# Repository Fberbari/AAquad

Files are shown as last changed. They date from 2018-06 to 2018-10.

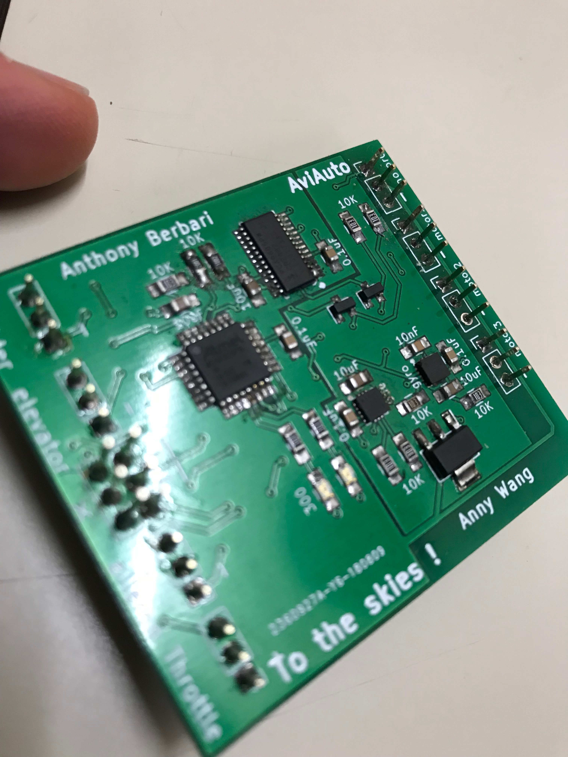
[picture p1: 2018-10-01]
pic_1.jpeg

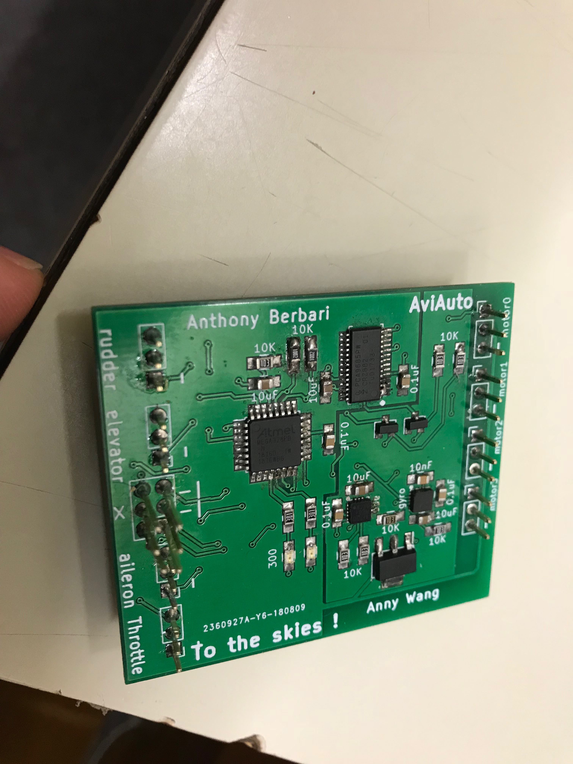
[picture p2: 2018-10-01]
pic_2.jpeg

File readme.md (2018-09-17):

This is an implementation of a quadcopter filght computer running baremetal on an atmega 328pb chip that takes input a standard hobby receiver and outputs pwm to esc's.

These directories contain the full firmware and the pcb design + gerber files.

As of right now, the system produces desirable results and has passed some basic functionality tests. 
I am currently waiting on a mechanical engineering student to finish designing the frame of the aircraft before further testing.

WORKING PRINCIPLE

	As of right now, the system reads input from the receiver via an interrupt based (asynchronous approach). This, because of the 50Hz pwm encoding that the receiver emits is by far the slowest process.

	Apart from this step, the rest of the processis synchronous and the loop goesas follows:

		1. The processor gathers data from the 2 on board sensors (accelerometer and gyroscope) via I2C.
		2. Using a modified version of the Kallman filter, the processor uses both pieces of data to determine the absolute position of the aircraft (with reference to gravity)
		3. A function gathers all the newest available data from the pilot and computes the pilots intention. (How should the aircraft bank and pitch and how strong should 		motor power be)
		4. A PID algorythim then uses the processed sensor data aswell, the processed pilot data and the previous cycle's data to compute 4 numbers that represent the 				percentage of full power that each motor should run at to best achieve the pilot's wishes
		5. Those numbers are encodedinto values that the pwm chip can understand and sent to it via I2C.
		6. The process repeats

PURPOSE

	The purose of this project was to familiarize myself with the basics of avr architecture, firmware design flow, communications between chips (I2C), pcb design flow etc.
	It was also a way to enter the world of embedded design in aviation. 

I (Anthony Berbari) AM SOLELY RESPONSIBLE FOR ALL THE FIRMWARE AND HARDWARE DESIGN DONE ON THIS PROJECT.

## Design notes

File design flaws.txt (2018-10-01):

1. each voltage regulator required a 10 uF cap

2. the footprints for the qfn's are far too small and the white squares are missing.

3. The back fin of the power egulators should be connected to the ground plane.

4. An IMU should have been used instead of a seperate acc and gyro.

5. Always use an external pullup resistor for the I2C lines. DO not rely on the software

6. Use the PWM pin todo mux sort of stuff.

7. ALWAYS select the cheapest and least complex approach.

8. The input capture unit (ICU) of the timers should be used to read pwm. 

9. use 2 different I2C busses when using a level shifter

10. spacing between header pins should fit a breadboard.

11. New and improved algos that you used in numerical analysys should be used to approximate the integral and derivative for the PID

NEgotiation genius principles+ECE 209 first lecture integrative thinking should be used

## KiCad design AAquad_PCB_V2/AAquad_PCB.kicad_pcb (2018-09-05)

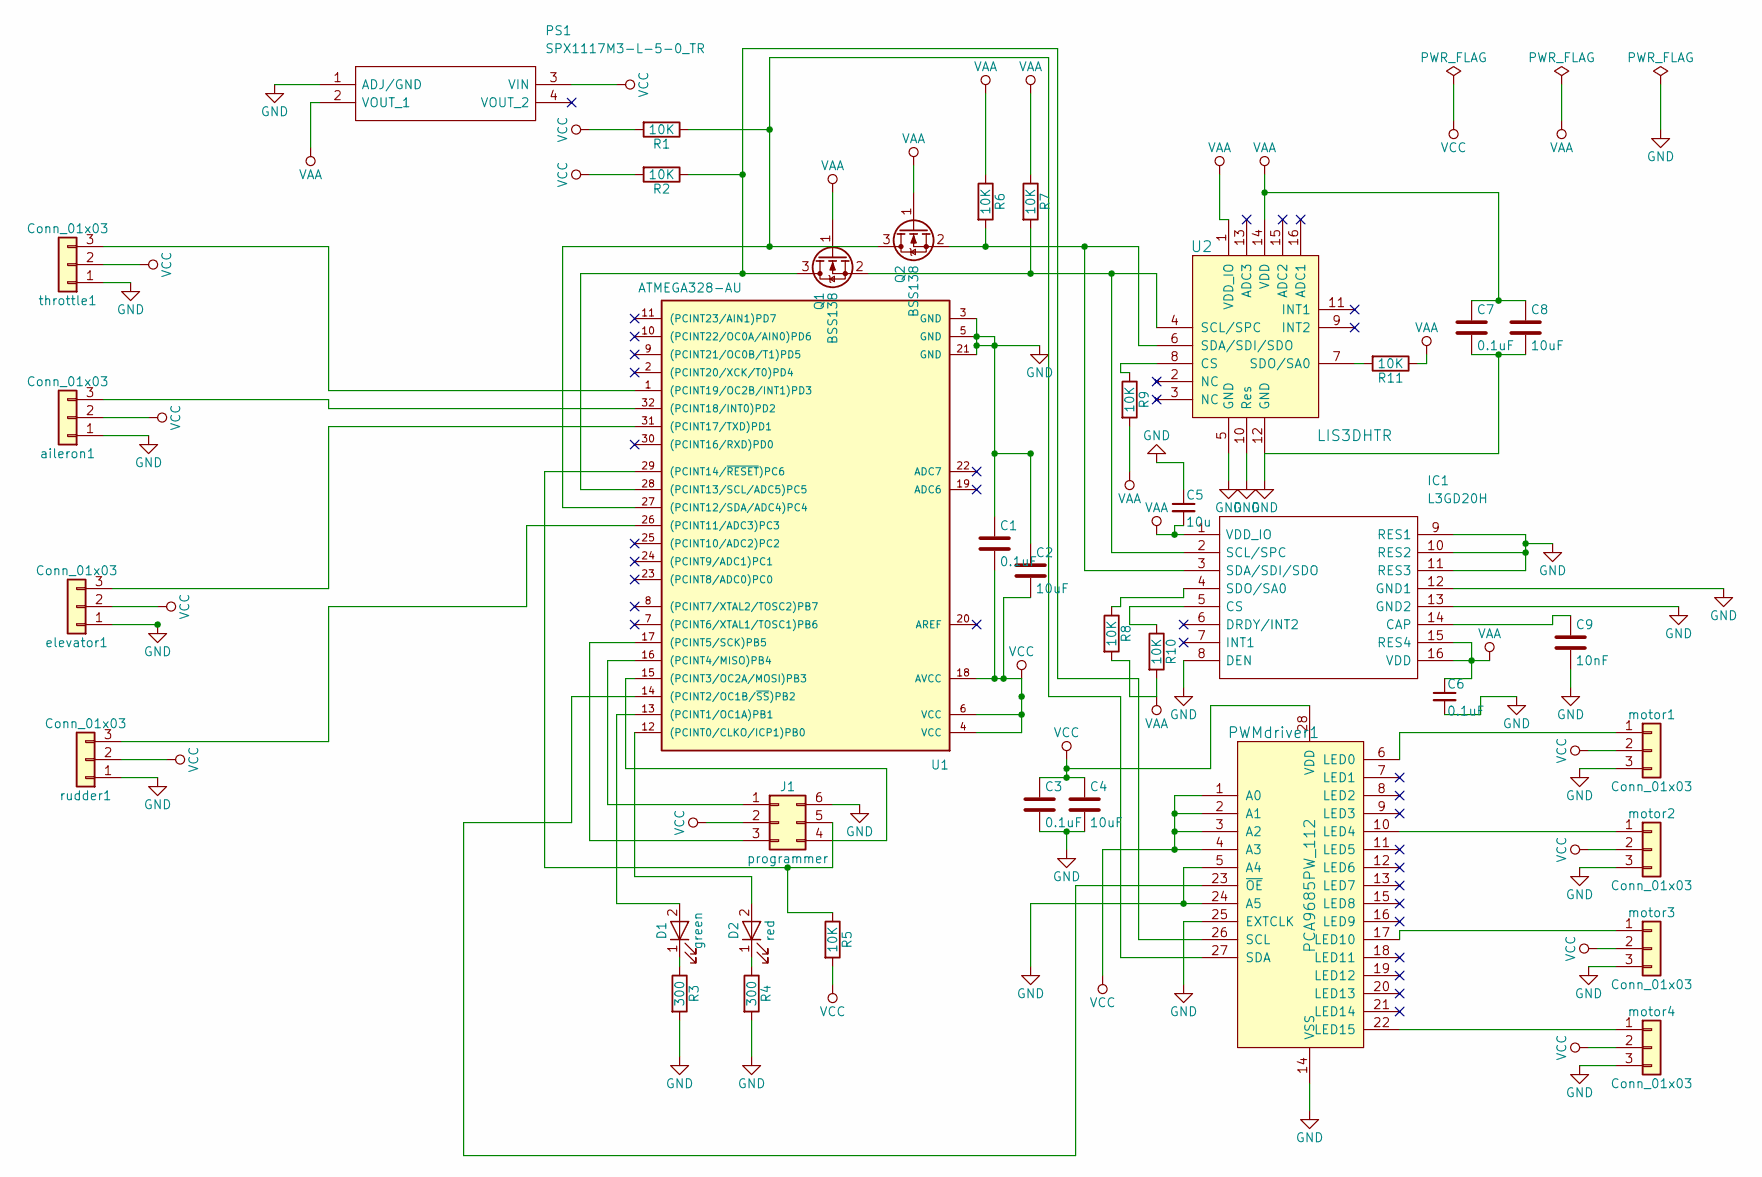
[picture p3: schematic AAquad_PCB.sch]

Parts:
C1, C3, C6, C7: 0.1uF; C_0805_HandSoldering
C2, C4, C8: 10uF; C_0805_HandSoldering
C5: 10u; C_0805_HandSoldering
C9: 10nF; C_0805_HandSoldering
D1: green; LED_0805_HandSoldering
D2: red; LED_0805_HandSoldering
IC1: L3GD20H; L3gd20h; Manufacturer_Part_Number L3GD20H
J1: programmer; Pin_Header_Straight_2x03_Pitch2.54mm
PS1: SPX1117M3-L-5-0_TR; SOT230P700X170-4N; Manufacturer_Part_Number SPX1117M3-L-5-0/TR
PWMdriver1: PCA9685PW_112; TSSOP-28_W4.40mm; MPN PCA9685PW,112; Digi-Key_PN 568-8366-5-ND
Q1, Q2: BSS138; SOT-23
R1, R2, R5, R6, R7, R8, R9, R10, R11: 10K; R_0805_HandSoldering
R3, R4: 300; R_0805_HandSoldering
U1: ATMEGA328-AU; TQFP-32_7x7mm_Pitch0.8mm
U2: LIS3DHTR; Lis3dh; MPN LIS3DHTR; Digi-Key_PN 497-10613-1-ND
aileron1: Conn_01x03; Pin_Header_Straight_1x03_Pitch2.54mm
elevator1: Conn_01x03; Pin_Header_Straight_1x03_Pitch2.54mm
motor1, motor2, motor3, motor4: Conn_01x03; Pin_Header_Straight_1x03_Pitch2.54mm
rudder1: Conn_01x03; Pin_Header_Straight_1x03_Pitch2.54mm
throttle1: Conn_01x03; Pin_Header_Straight_1x03_Pitch2.54mm

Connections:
GND: C1.1, C2.1, C3.2, C4.2, C5.1, C6.2, C7.2, C8.2, C9.2, IC1.8 (DEN), IC1.9 (RES1), IC1.10 (RES2), IC1.11 (RES3), IC1.12 (GND1), IC1.13 (GND2), J1.6, PS1.1 (ADJ/GND), PWMdriver1.5 (A4), PWMdriver1.14 (VSS), PWMdriver1.24 (A5), PWMdriver1.25 (EXTCLK), R3.2, R4.2, U1.3 (GND), U1.5 (GND), U1.21 (GND), U2.5 (GND), U2.10 (Res), U2.12 (GND), aileron1.1, elevator1.1, motor1.3, motor2.3, motor3.3, motor4.3, rudder1.1, throttle1.1
unnamed: C9.1, IC1.14 (CAP)
unnamed: D1.1 (K), R3.1
unnamed: D1.2 (A), U1.13 ((PCINT1/OC1A)PB1)
unnamed: D2.1 (K), R4.1
unnamed: D2.2 (A), U1.12 ((PCINT0/CLKO/ICP1)PB0)
unnamed: IC1.2 (SCL/SPC), Q1.2 (S), R7.2, U2.4 (SCL/SPC)
unnamed: IC1.3 (SDA/SDI/SDO), Q2.2 (S), R6.2, U2.6 (SDA/SDI/SDO)
unnamed: IC1.4 (SDO/SA0), R8.1
unnamed: IC1.5 (CS), R10.1
unnamed: J1.1, U1.16 ((PCINT4/MISO)PB4)
unnamed: J1.3, U1.17 ((PCINT5/SCK)PB5)
unnamed: J1.4, U1.15 ((PCINT3/OC2A/MOSI)PB3)
unnamed: J1.5, R5.1, U1.29 ((PCINT14/~RESET~)PC6)
unnamed: PWMdriver1.6 (LED0), motor1.1
unnamed: PWMdriver1.10 (LED4), motor2.1
unnamed: PWMdriver1.17 (LED10), motor3.1
unnamed: PWMdriver1.22 (LED15), motor4.1
unnamed: PWMdriver1.23 (~OE), U1.14 ((PCINT2/OC1B/~SS~)PB2)
unnamed: PWMdriver1.26 (SCL), Q1.3 (D), R2.1, U1.28 ((PCINT13/SCL/ADC5)PC5)
unnamed: PWMdriver1.27 (SDA), Q2.3 (D), R1.1, U1.27 ((PCINT12/SDA/ADC4)PC4)
unnamed: R9.1, U2.8 (CS)
unnamed: R11.2, U2.7 (SDO/SA0)
unnamed: U1.1 ((PCINT19/OC2B/INT1)PD3), throttle1.3
unnamed: U1.26 ((PCINT11/ADC3)PC3), rudder1.3
unnamed: U1.31 ((PCINT17/TXD)PD1), elevator1.3
unnamed: U1.32 ((PCINT18/INT0)PD2), aileron1.3
VAA: C5.2, C6.1, C7.1, C8.1, IC1.1 (VDD_IO), IC1.15 (RES4), IC1.16 (VDD), PS1.2 (VOUT_1), Q1.1 (G), Q2.1 (G), R6.1, R7.1, R8.2, R9.2, R10.2, R11.1, U2.1 (VDD_IO), U2.14 (VDD)
VCC: C1.2, C2.2, C3.1, C4.1, J1.2, PS1.3 (VIN), PWMdriver1.1 (A0), PWMdriver1.2 (A1), PWMdriver1.3 (A2), PWMdriver1.4 (A3), PWMdriver1.28 (VDD), R1.2, R2.2, R5.2, U1.4 (VCC), U1.6 (VCC), U1.18 (AVCC), aileron1.2, elevator1.2, motor1.2, motor2.2, motor3.2, motor4.2, rudder1.2, throttle1.2

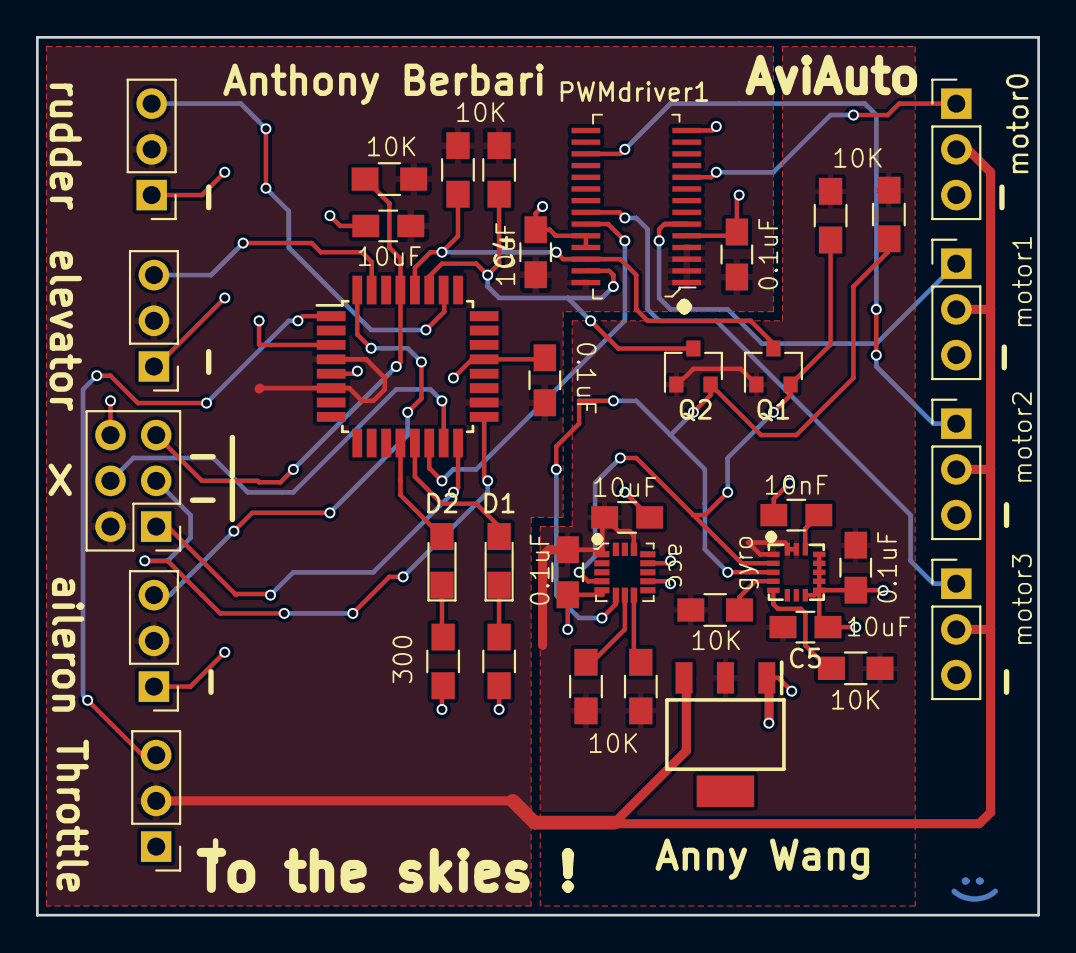
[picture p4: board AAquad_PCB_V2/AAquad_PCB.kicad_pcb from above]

Board: 2 copper layers, 55.6 x 48.8 mm, 38 parts (0 on the bottom side), 29 nets.

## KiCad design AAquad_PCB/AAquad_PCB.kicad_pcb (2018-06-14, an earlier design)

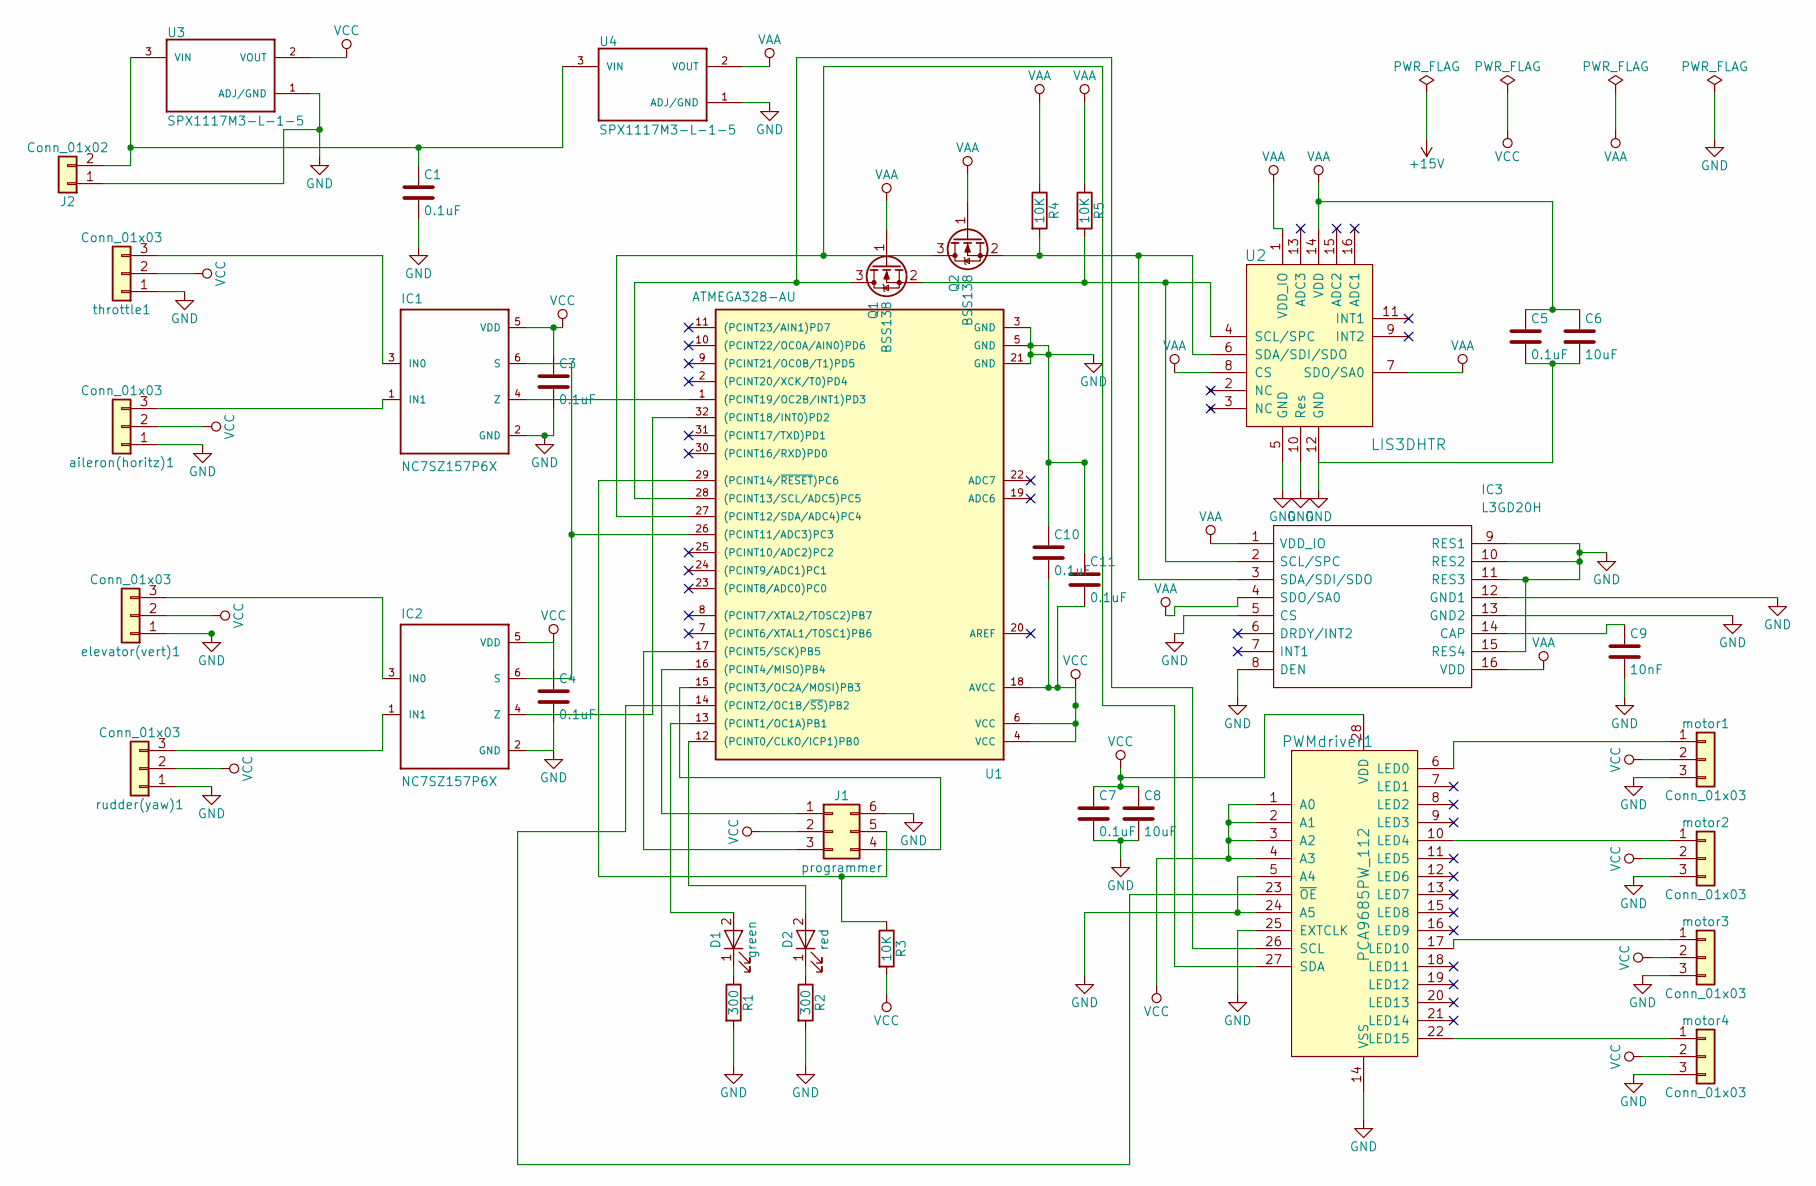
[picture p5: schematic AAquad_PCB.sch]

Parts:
C1, C3, C4, C5, C7, C10, C11: 0.1uF; C_0805_HandSoldering
C6, C8: 10uF; C_0805_HandSoldering
C9: 10nF; C_0805_HandSoldering
D1: green; LED_0805_HandSoldering
D2: red; LED_0805_HandSoldering
IC1, IC2: NC7SZ157P6X; SOT65P210X110-6N
IC3: L3GD20H; LGA(3X3X1.0-16L); Manufacturer_Part_Number L3GD20H
J1: programmer; Pin_Header_Angled_2x03_Pitch2.54mm
J2: Conn_01x02; Pin_Header_Angled_1x02_Pitch2.54mm
PWMdriver1: PCA9685PW_112; TSSOP-28_W4.40mm; MPN PCA9685PW,112; Digi-Key_PN 568-8366-5-ND
Q1, Q2: BSS138; SOT-23
R1, R2: 300; R_0805_HandSoldering
R3, R4, R5: 10K; R_0805_HandSoldering
U1: ATMEGA328-AU; TQFP-32_7x7mm_Pitch0.8mm
U2: LIS3DHTR; VFLGA-16_3x3mm; MPN LIS3DHTR; Digi-Key_PN 497-10613-1-ND
U3, U4: SPX1117M3-L-1-5; SOT230P700X180-3N
aileron(horitz)1: Conn_01x03; Pin_Header_Angled_1x03_Pitch2.54mm
elevator(vert)1: Conn_01x03; Pin_Header_Angled_1x03_Pitch2.54mm
motor1, motor2, motor3, motor4: Conn_01x03; Pin_Header_Angled_1x03_Pitch2.54mm
rudder(yaw)1: Conn_01x03; Pin_Header_Angled_1x03_Pitch2.54mm
throttle1: Conn_01x03; Pin_Header_Angled_1x03_Pitch2.54mm

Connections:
GND: C1.2, C3.2, C4.2, C5.2, C6.2, C7.2, C8.2, C9.2, C10.1, C11.1, IC1.2 (GND), IC2.2 (GND), IC3.5 (CS), IC3.8 (DEN), IC3.9 (RES1), IC3.10 (RES2), IC3.11 (RES3), IC3.12 (GND1), IC3.13 (GND2), IC3.15 (RES4), J1.6, J2.1, PWMdriver1.5 (A4), PWMdriver1.14 (VSS), PWMdriver1.24 (A5), PWMdriver1.25 (EXTCLK), R1.2, R2.2, U1.3 (GND), U1.5 (GND), U1.21 (GND), U2.5 (GND), U2.10 (Res), U2.12 (GND), U3.1 (ADJ/GND), U4.1 (ADJ/GND), aileron(horitz)1.1, elevator(vert)1.1, motor1.3, motor2.3, motor3.3, motor4.3, rudder(yaw)1.1, throttle1.1
unnamed: C1.1, J2.2, U3.3 (VIN), U4.3 (VIN)
unnamed: C9.1, IC3.14 (CAP)
unnamed: D1.1 (K), R1.1
unnamed: D1.2 (A), U1.13 ((PCINT1/OC1A)PB1)
unnamed: D2.1 (K), R2.1
unnamed: D2.2 (A), U1.12 ((PCINT0/CLKO/ICP1)PB0)
unnamed: IC1.1 (IN1), aileron(horitz)1.3
unnamed: IC1.3 (IN0), throttle1.3
unnamed: IC1.4 (Z), U1.1 ((PCINT19/OC2B/INT1)PD3)
unnamed: IC1.6 (S), IC2.6 (S), U1.26 ((PCINT11/ADC3)PC3)
unnamed: IC2.1 (IN1), rudder(yaw)1.3
unnamed: IC2.3 (IN0), elevator(vert)1.3
unnamed: IC2.4 (Z), U1.32 ((PCINT18/INT0)PD2)
unnamed: IC3.2 (SCL/SPC), Q1.2 (S), R5.2, U2.4 (SCL/SPC)
unnamed: IC3.3 (SDA/SDI/SDO), Q2.2 (S), R4.2, U2.6 (SDA/SDI/SDO)
unnamed: J1.1, U1.16 ((PCINT4/MISO)PB4)
unnamed: J1.3, U1.17 ((PCINT5/SCK)PB5)
unnamed: J1.4, U1.15 ((PCINT3/OC2A/MOSI)PB3)
unnamed: J1.5, R3.1, U1.29 ((PCINT14/~RESET~)PC6)
unnamed: PWMdriver1.6 (LED0), motor1.1
unnamed: PWMdriver1.10 (LED4), motor2.1
unnamed: PWMdriver1.17 (LED10), motor3.1
unnamed: PWMdriver1.22 (LED15), motor4.1
unnamed: PWMdriver1.23 (~OE), U1.14 ((PCINT2/OC1B/~SS~)PB2)
unnamed: PWMdriver1.26 (SCL), Q1.3 (D), U1.28 ((PCINT13/SCL/ADC5)PC5)
unnamed: PWMdriver1.27 (SDA), Q2.3 (D), U1.27 ((PCINT12/SDA/ADC4)PC4)
VAA: C5.1, C6.1, IC3.1 (VDD_IO), IC3.4 (SDO/SA0), IC3.16 (VDD), Q1.1 (G), Q2.1 (G), R4.1, R5.1, U2.1 (VDD_IO), U2.7 (SDO/SA0), U2.8 (CS), U2.14 (VDD), U4.2 (VOUT)
VCC: C3.1, C4.1, C7.1, C8.1, C10.2, C11.2, IC1.5 (VDD), IC2.5 (VDD), J1.2, PWMdriver1.1 (A0), PWMdriver1.2 (A1), PWMdriver1.3 (A2), PWMdriver1.4 (A3), PWMdriver1.28 (VDD), R3.2, U1.4 (VCC), U1.6 (VCC), U1.18 (AVCC), U3.2 (VOUT), aileron(horitz)1.2, elevator(vert)1.2, motor1.2, motor2.2, motor3.2, motor4.2, rudder(yaw)1.2, throttle1.2

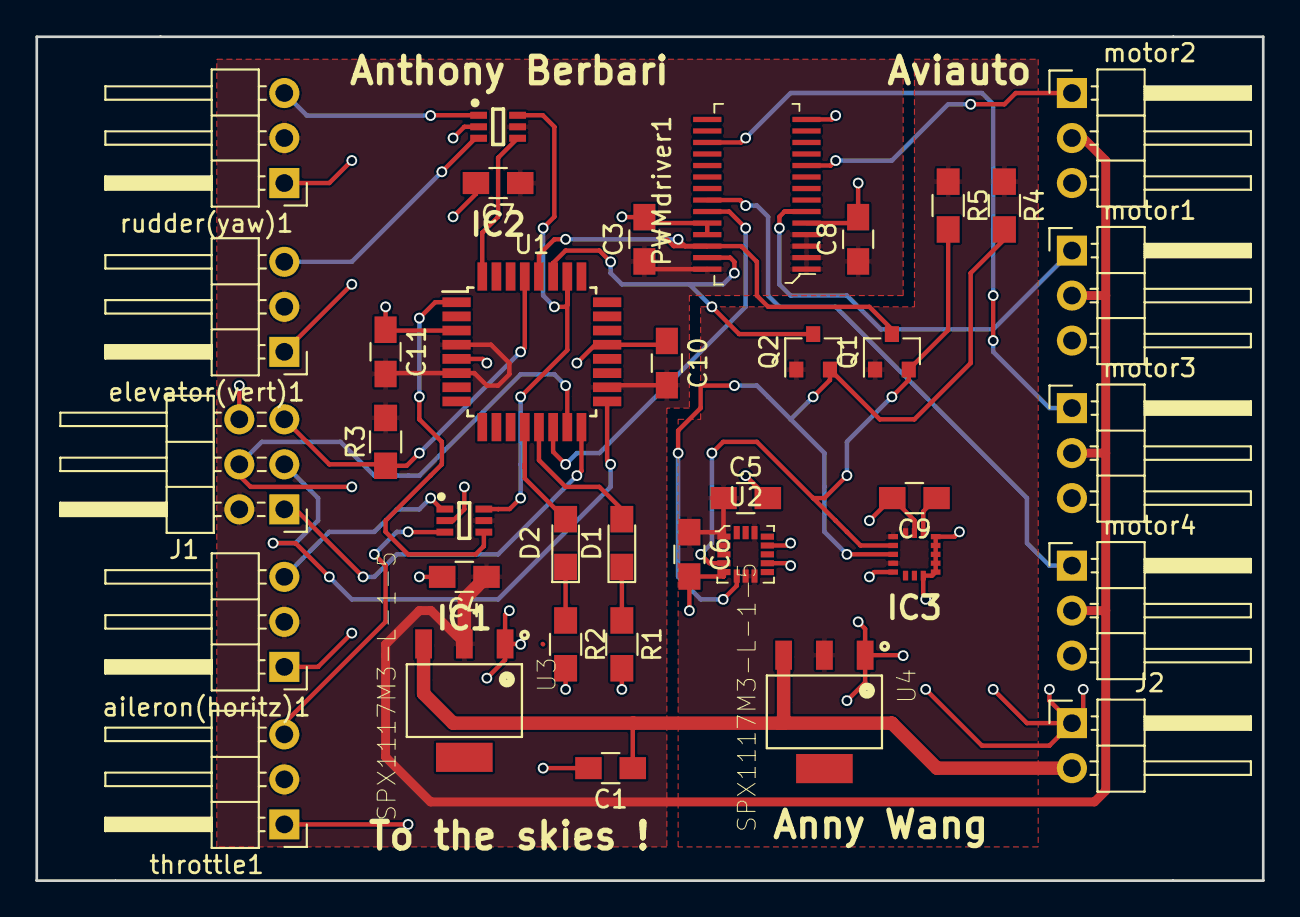
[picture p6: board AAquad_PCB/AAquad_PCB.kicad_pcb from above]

Board: 2 copper layers, 69.2 x 47.6 mm, 37 parts (0 on the bottom side), 29 nets.

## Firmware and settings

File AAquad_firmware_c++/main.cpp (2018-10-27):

/*
 * Firmware Developer : Anthony Berbari
 */ 

#include "avr_compiler.h"



#include "pwm_in_vars.h"	// global external variables



#include "init.h"
#include "I2C_328pb.h"
#include "pilot_instructions.h"
#include "pwm_chip.h"
#include "sensors.h"
#include "bp_PID.h"
#include "combine_data.h"


	
	// These global vars hold raw pilot data. 
	// Requested... holds the time between a rise and fall (or fall and rise). unit used is arbitrary, so long as all is consistent
	// these variables are declared in pwm_in_vars.h and that file is include in main.cpp and in the pilot_instructions.h class
	volatile uint16_t requested_aileron_pos = 0;
	volatile uint16_t requested_elevator_pos = 0;
	volatile uint16_t requested_rudder_pos = 0;
	volatile uint16_t requested_throttle_pos = 0;

	// these store the time stamp of the previous time the associated ISR triggered
	// substracting the time stamp of the previous edge from that of the current edge allows the algorythim to obtain a measure of the pwm's duty cycle.
	// that measure is stored in the above requested.... variables
	volatile uint16_t temp_timer_aileron = 0;
	volatile uint16_t temp_timer_elevator = 0; 
	volatile uint16_t temp_timer_rudder = 0;
	volatile uint16_t temp_timer_throttle = 0; 

	// these are flags that are set true right after the ISR's gather new pilot data
	// they ensure the algorythim that processes it is infact dealing with fresh data
	volatile bool new_aileron_data_available = false;
	volatile bool new_elevator_data_available = false;
	volatile bool new_rudder_data_available = false;
	volatile bool new_throttle_data_available = false;


	// pid objects declaired here to be visible to the ISR
	 pid bank_pid;
	 pid pitch_pid;

	// these global vars are used to exchange data between the ISR that contains the pid algorythim and the main while(1) loop
	volatile float bank_number = 0;
	volatile float pitch_number = 0;
	volatile float throttle_percentage = 0;
	volatile bool  pid_called = false;
	
	


int main(void){
	
	// points to the array that stores the percentage of full each motor should run at
	volatile int* volatile motor_percentages;
	
	
	initialize::timers();
	initialize::interrupts();
	
	// gathers and processes the pilot's wishes
	pilot_instructions pilot;
	pilot.set_max_angle(30);
	pilot.set_max_yaw_rate(45);
	
	//handles all sensor data gathering and processing
	sensors sense;
	
	// initialisation of the chip responsible for talking directly to the esc's
	pwm_chip pwm(121);


	// processes current position and requested position into a number proportional to motor strength
	// This is only for the bank (tilted left or right) angle
	bank_pid.setWeights(1,1,0.5);
	bank_pid.setOutputLimits(-50, 50);

	//Same as on top but for the pitch (tilted forward or back) angle
	pitch_pid.setWeights(1,1,0.5);
	pitch_pid.setOutputLimits(-50, 50);
	


	

	
	// Initialisation finished. Interupts enabled, ready to begin
	sei();
	

	
	while(1){
		
		// sensor data gathered
		sense.read_acc();
		sense.read_gyro();
			
		// all sensor data received and processed
		sense.compute_position();
	
		// all pilot data received and processed
		pilot.compute();	
	
		// pilot commands and sensor data passed to PID object
		pitch_pid.setPoints(pilot.get_pitch_angle(), sense.get_pitch());		
		bank_pid.setPoints(pilot.get_bank_angle(), sense.get_roll());

		//computiations are done
		// the contents of bank_number, pitch_number and throttle power are representative of the pitch and bank required to achieve pilot's wishes
		// these vars are ready to be used by the combine_data method, once the ISR calls it.
		throttle_percentage = pilot.get_throttle_power();
			
		// data_available is only true after a call of the pid loop from the interrupt
		// it is then immediately set to false in wait of the next interrupt	
		if (pid_called){
			
			// results of pid are combined and translated into percentages
			// motor points to an array that contains the percentages that each motor should be run at.
			motor_percentages = combine(bank_number, pitch_number, throttle_percentage);
			
			// data encoded into PWM chip language and sent to the esc's
			pwm.pass( (int*) motor_percentages);	
			pid_called = false;
		}

	}



return 0;

}


ISR(TIMER0_COMPA_vect){

	// PID output recomputed every 0.1s	

		// get the numbers proportional to how strongly we must attempt to bank and pitch to achieve th pilot's wishes 
		bank_number = bank_pid.refresh();
		pitch_number = pitch_pid.refresh();

		// set the flag 
		pid_called = true;
}



// comments for the 4 ISR's to come are the same, so they are only included on this one
// All the following ISR's trigger on any edge
ISR(INT0_vect){
	
		// store the timestamp of the time the edge was detected
		uint16_t temp = TCNT1;
		
		// obviously, the previous edge must have happened before the current edge
		// but because the 16 bit timer may have overflowed and started the count back from 0, we need to check for this
		if ( temp < temp_timer_aileron){

			// the math inside the if condition accounts for a timer overflow
			// the comparison ensures that we only take in new data if that data is reasonable, so  as to not corrupt down the stream algorythyms
			// the values 1110 and 2000 are the lower and upper bounds on what the receiver can output
			if ( ((0xffff - temp_timer_aileron + temp) < 2000) && ((0xffff - temp_timer_aileron + temp) > 1110)){
				
				requested_aileron_pos = (0xffff - temp_timer_aileron) + temp ;

				// since the latest requested aileron position has just been updated, set the flag to true
				new_aileron_data_available = true;
			}
		}

		// this else statement catches the case were no timer overflow has occured
		else {
			
			// the comparisons ensure that we only take in new data if that data is reasonable, so  as to not corrupt down the stream algorythyms
			// the values 1110 and 2000 are the lower and upper bounds on what the receiver can output
			if ( ( (temp - temp_timer_aileron) < 2000) && ( (temp - temp_timer_aileron) > 1110) ) {
	
				requested_aileron_pos = temp - temp_timer_aileron;

				// since the latest requested aileron position has just been updated, set the flag to true
				new_aileron_data_available = true;
			
			}
		}
	
		// no matter what, the current timestamp becomes the previous timestamp
		temp_timer_aileron = temp;

}

ISR(INT1_vect){
	
		uint16_t temp = TCNT1;
		

		if ( temp < temp_timer_throttle){


			if ( ((0xffff - temp_timer_throttle + temp) < 2000) && ((0xffff - temp_timer_throttle + temp) > 1015)){
						
				requested_throttle_pos = (0xffff - temp_timer_throttle) + temp ;
				new_throttle_data_available = true;
			}
		}

		else {
	

			if ( ( (temp - temp_timer_throttle) < 2000) && ( (temp - temp_timer_throttle) > 1015) ) {
						
				requested_throttle_pos = temp - temp_timer_throttle;
				new_throttle_data_available = true;
							
			}
			
		}
	
		
		temp_timer_throttle = temp;
		
		
		
}



ISR(PCINT1_vect){

	uint16_t temp = TCNT1;
		

	if ( temp < temp_timer_rudder){	


		if ( ((0xffff - temp_timer_rudder + temp) < 2000) && ((0xffff - temp_timer_rudder + temp) > 1110)){
						
			requested_rudder_pos = (0xffff - temp_timer_rudder) + temp;
			new_rudder_data_available = true;
		}
	}

	else {	


		if ( ( (temp - temp_timer_rudder) < 2000) && ( (temp - temp_timer_rudder) > 1110) ){
						
			requested_rudder_pos = temp - temp_timer_rudder;
			new_rudder_data_available = true;
						
		}
		
	}

	
	temp_timer_rudder = temp;
	
	

}

ISR(PCINT2_vect){

	uint16_t temp = TCNT1;
	

	if ( temp < temp_timer_elevator){


		if ( ((0xffff - temp_timer_elevator + temp) < 2000) && ((0xffff - temp_timer_elevator + temp) > 1110)){
						
			requested_elevator_pos = (0xffff - temp_timer_elevator) + temp;
			new_elevator_data_available = true;
		}
	}

	else {

		if ( ( (temp - temp_timer_elevator) < 2000) && ( (temp - temp_timer_elevator) > 1110) ) {
						
			requested_elevator_pos = temp - temp_timer_elevator;
			new_elevator_data_available = true;
						
		}
		
	}

	
	temp_timer_elevator = temp;
	
	

}

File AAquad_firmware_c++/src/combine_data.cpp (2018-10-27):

#include "combine_data.h"


int* combine(float bank_number, float pitch_number, float throttle_percentage){

	// the top one is temporary for processing floats whilethe bottom stores the ints
	// bottom one is the one that returns
	float motor[4];
	static int ret_motor[4];

	//inex of motor heavily depends on how the accelerometer and gyro are pointed and how the motors are plugged in.
	motor[0] = (bank_number + pitch_number)  / 2 ;
	motor[1] = (bank_number - pitch_number)  / 2 ;
	motor[2] = (-bank_number + pitch_number) / 2 ;
	motor[3] = (-bank_number - pitch_number) / 2 ;
	
	
	// numbers were in the range [-50, 50], this effectively turns them into a percentage
	// that percentage is the percentage of full power that each motor should turn at.
	for (int i = 0; i < 4; i++){
		
		motor[i] += 50;
	}

	
	// now, that themotors are working correctly relative to each other, multiply by throttle percentage to get the absolute values.
	for (int i = 0; i < 4; i++){
		
		motor[i] *= (throttle_percentage / 80);
	}

	
	// these floats will be cast to integers, so round before hand
	for (int i = 0; i < 4; i++){
		
		ret_motor[i] = round(motor[i]);
	}
	
	
	
	return  ret_motor;

}

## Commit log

2018-07-15 added cart
    [parts(includes_Buzzerboxes).csv]
2018-07-18 built the mux timer init function
2018-07-31 fixed pwm read
2018-08-01 fixed pwm read and fixed timer controll
2018-08-03 interfacing with PWM chip
2018-08-06 began to work on the translating motors branch
2018-08-07 successfull read and processing of PWM on ext_int0
2018-08-22 built PCB revision 2
    [AAquad_PCB.kicad_pcb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]
2018-08-22 added accelerometer functon
2018-08-24 creation of gyro_init and advances on interrupts in main
2018-08-27 sensor data processing
2018-08-28 installed and updated the PID class
2018-09-01 working on PID class and integration with the whole app
2018-09-03 properly and accurately reading pilot pwm on ext int 0
2018-09-03 succesfull conversion of throttle power to percentage
2018-09-05 properly reading all channels
    [AAquad_PCB.kicad_pcb]
2018-09-05 properly communicating with acc and gyro
2018-09-06 acc + gyro data successfully combined to report angle
2018-09-06 PID algorythym functioning properly
2018-09-12 improved filtering
2018-09-13 ignored some directories
    [familylist_refdes.csv, parts(includes_Buzzerboxes).csv]
2018-10-16 upgraded to use bullet proof pid class
2018-10-27 called pid from timer interrupt
